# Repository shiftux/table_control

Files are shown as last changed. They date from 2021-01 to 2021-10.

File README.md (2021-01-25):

# Automating an electric standing desk
The perfect ergonomic desk solution for your prolonged home office during Covid.

Check out my article for a detailed description of the project [https://shiftux.org/making_projects/standing_desk.html](https://shiftux.org/making_projects/standing_desk.html)
### Intro
I have an electric desk that I can move from a sitting to a standing position. However I have to keep pressing a button for around 15 seconds, and then never really know exactly where to stop, since there is no top or bottom reference, except my feeling. Needless to say I decided to automate this.

### Project Video
Standing Desk Automation (https://www.youtube.com/watch?v=ZzHkn_32jh8 "Standing Desk Automation")

### State Machine
I implemented a state machine using 5 states. Where "Moving Up/Down" is used when the buttons are manually pressed (move the table a bit) and "Shift Up/Down" is used to move the table to either the top or bottom position.

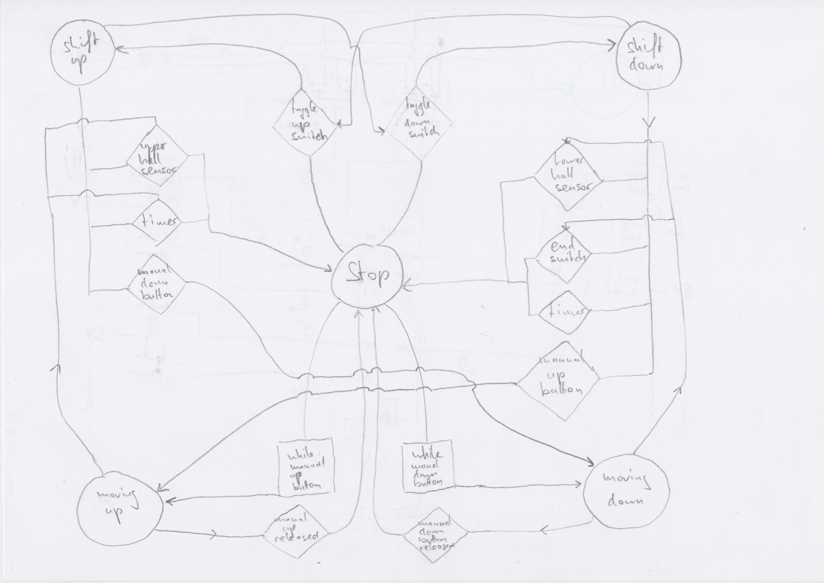
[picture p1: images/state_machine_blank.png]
The State Machine State Machine


### Wiring diagram
The wiring diagram is pretty straight forward using pull down resistors where required to prevent the Arduino from getting floating / noisy input.

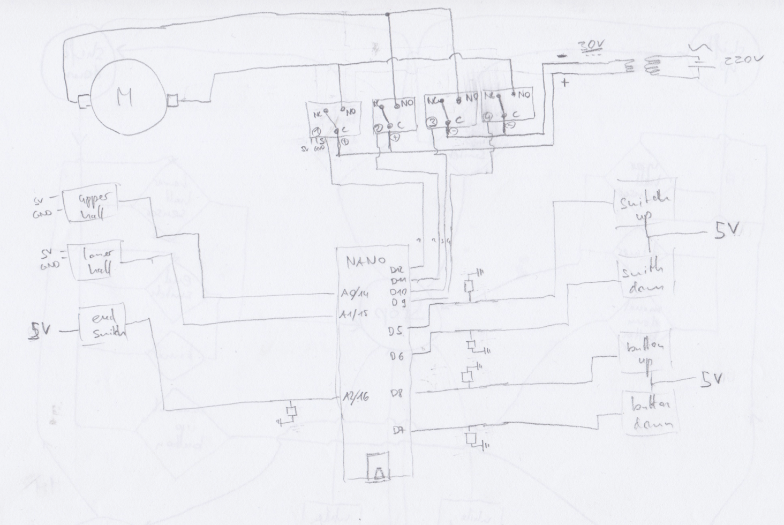
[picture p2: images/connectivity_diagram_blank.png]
The Wiring Diagram Wiring Diagram


### Components used
- 1x electric Table (and its buttons)
- 4x [Relais](https://www.conrad.ch/de/p/makerfactory-relais-modul-mf-6402384-1-st-passend-fuer-arduino-2134128.html)
- 2x [Hall sensor](https://www.conrad.ch/de/p/iduino-1485327-hallsensor-passend-fuer-einplatinen-computer-arduino-1485327.html)
- 1x [Arduino Nano](https://www.aliexpress.com/item/4000112750588.html?spm=a2g0s.9042311.0.0.27424c4dbc3uKd)
- 4x [Magnets](https://www.conrad.ch/de/p/tru-components-1572118-permanent-magnet-rund-x-h-5-mm-x-2-mm-n35eh-1-18-1-2-t-grenztemperatur-max-200-c-1572118.html)
- 1x [Switch](https://www.conrad.ch/de/p/apem-5239a-52390003-kippschalter-250-v-ac-3-a-1-x-ein-aus-ein-rastend-0-rastend-1-st-700179.html)
- 1x [Micro switch as End Switch](https://www.conrad.de/de/p/marquardt-mikroschalter-1050-5202-250-v-ac-5-a-1-x-ein-ein-tastend-1-st-703137.html)
- Loads of [DuPont Connectors](https://www.aliexpress.com/item/4000570942676.html?spm=a2g0s.9042311.0.0.27424c4dosd7NR)
- 5 10kO Resistors (pull down)
- Cable (small diameter for all the electronics and a bit larger for the relais and motor power)
- Couple of small screws
- Some of 3D printed parts (in the CAD folder)
- Micro USB Cable + Power adapter for the Arduino

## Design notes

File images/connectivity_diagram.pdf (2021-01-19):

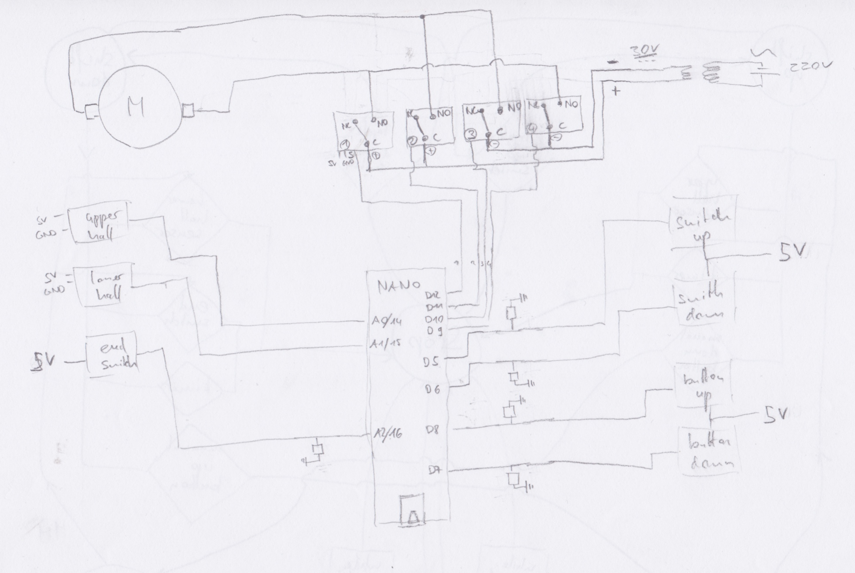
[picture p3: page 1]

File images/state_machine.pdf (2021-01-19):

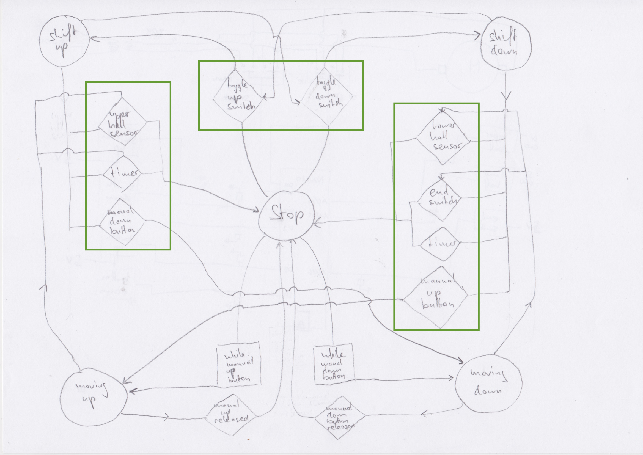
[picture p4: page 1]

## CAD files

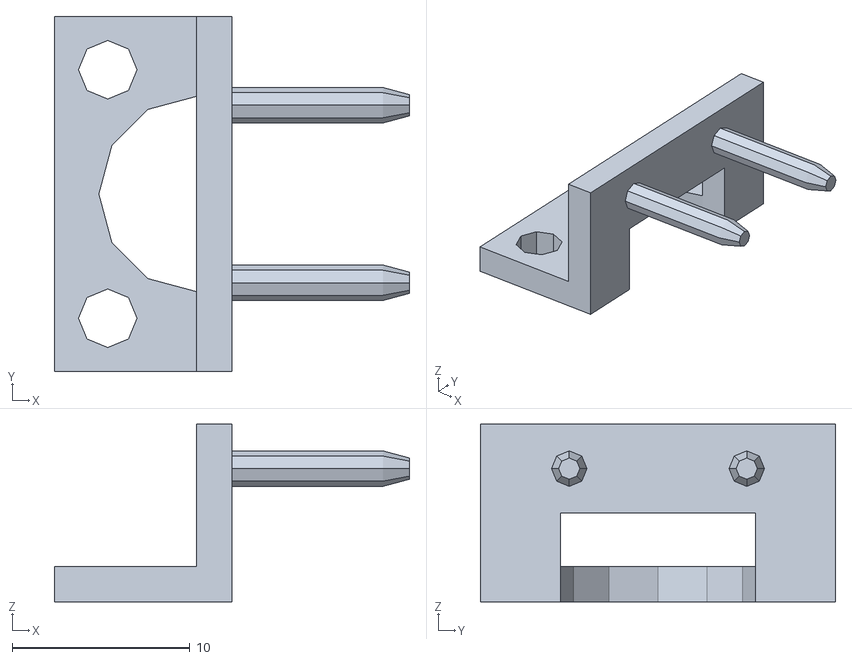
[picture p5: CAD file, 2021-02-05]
CAD/switch_holder_male.stl
20.0 x 20.0 x 10.0

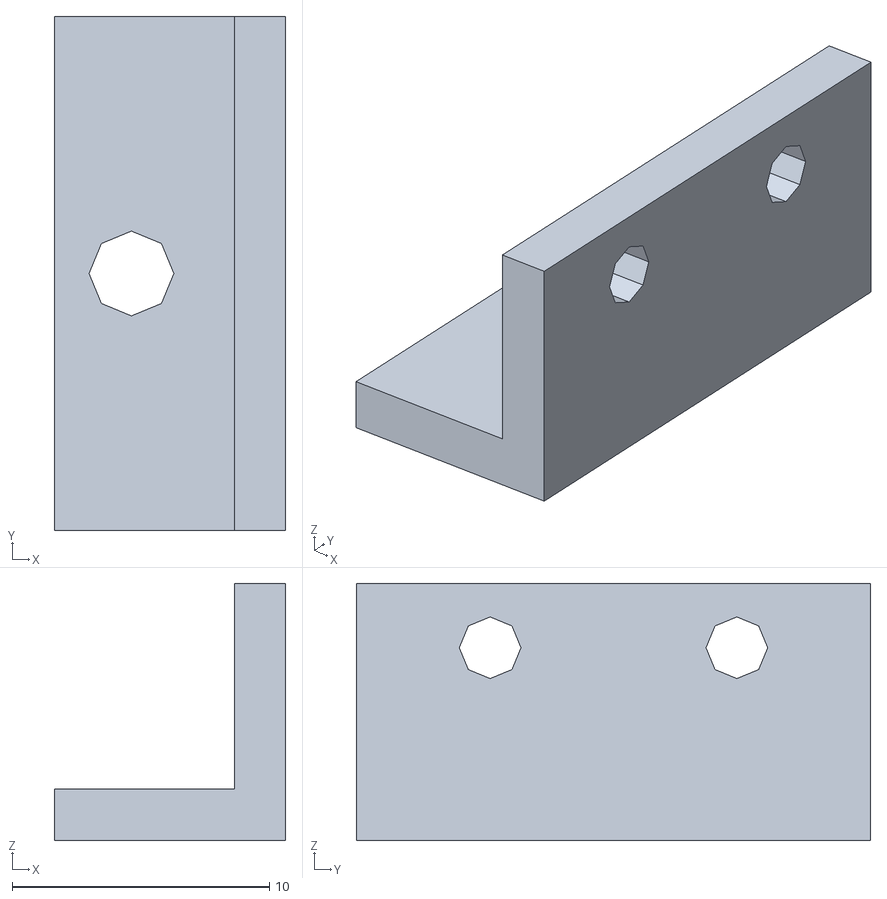
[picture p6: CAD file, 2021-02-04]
CAD/switch_holder_feemale.stl
9.00 x 20.0 x 10.0

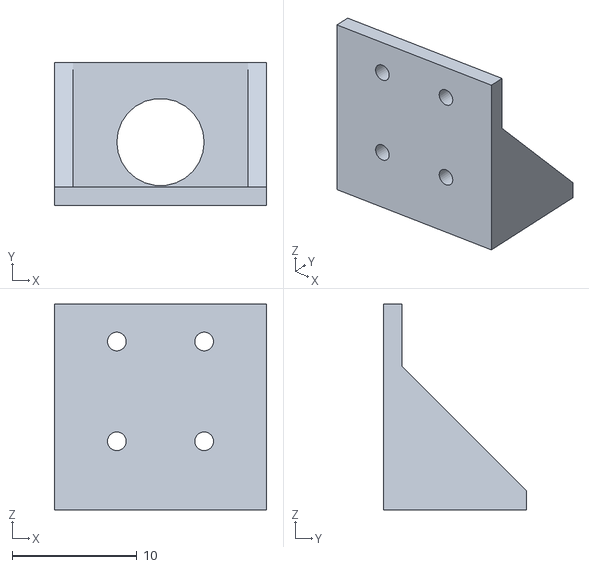
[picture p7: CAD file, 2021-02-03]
CAD/switch_holder.stl
17.0 x 11.5 x 16.5

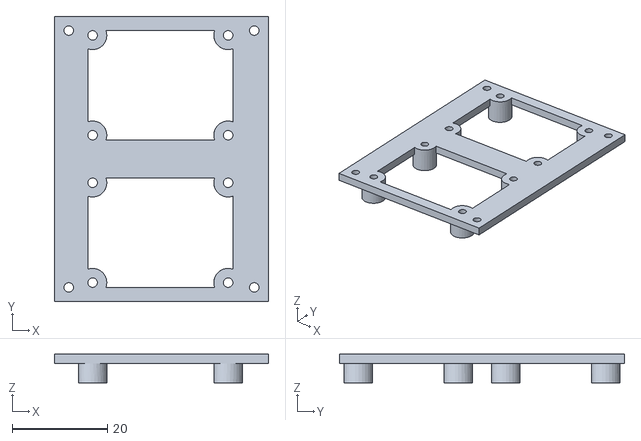
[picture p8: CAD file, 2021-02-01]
CAD/relais_holder.stl
45.0 x 60.0 x 6.00

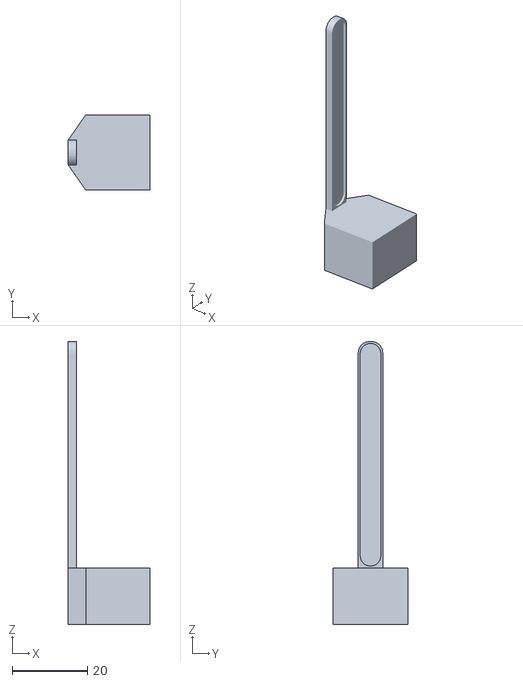
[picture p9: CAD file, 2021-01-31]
CAD/magnet_holder_lower.stl
21.7 x 20.0 x 75.0

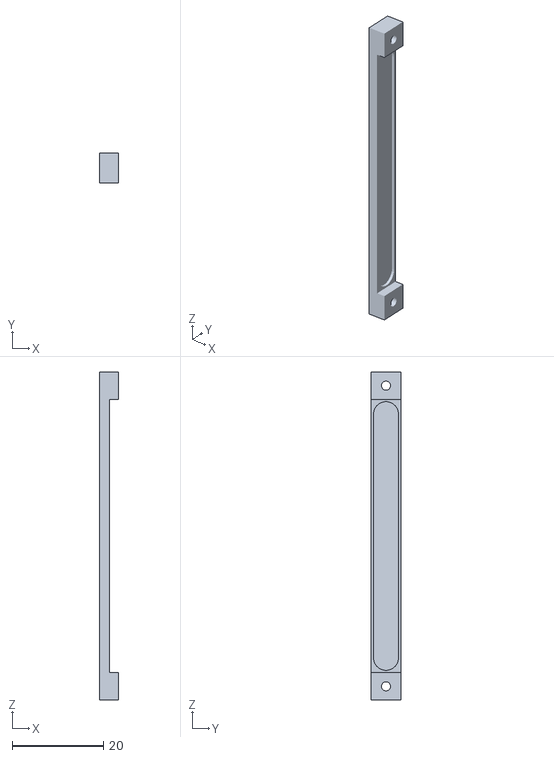
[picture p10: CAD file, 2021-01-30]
CAD/magnet_holder.stl
4.20 x 6.50 x 72.0

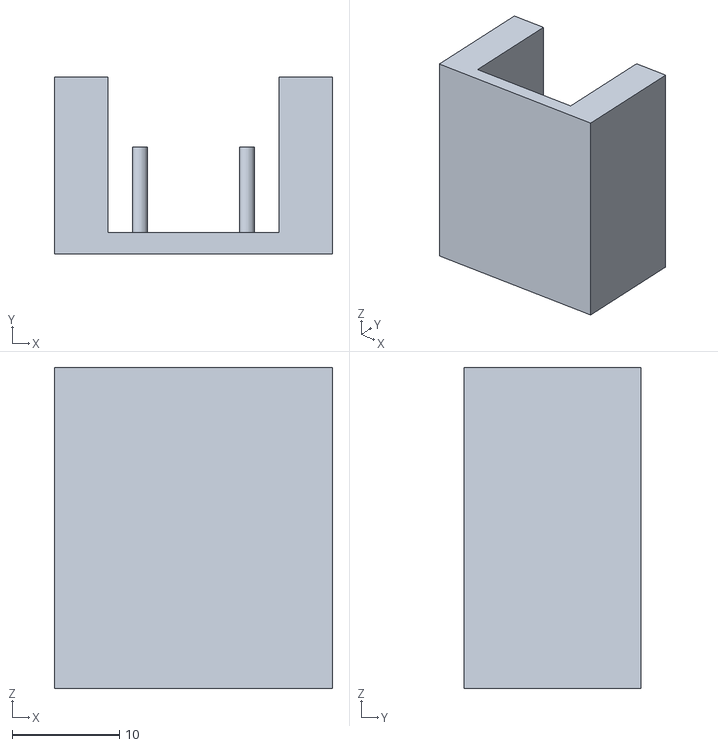
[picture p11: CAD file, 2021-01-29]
CAD/hall_sensor_holder_lower.stl
26.0 x 16.5 x 30.0

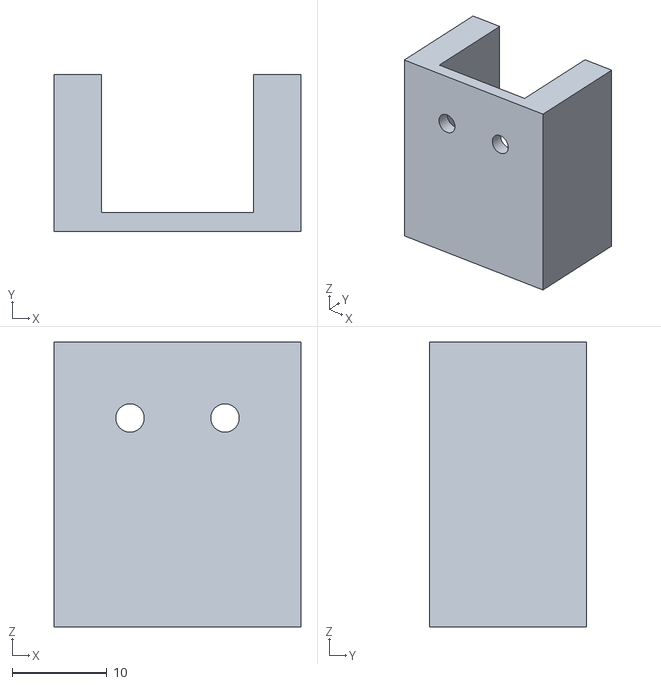
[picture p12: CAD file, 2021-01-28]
CAD/hall_sensor_holder.stl
26.0 x 16.5 x 30.0

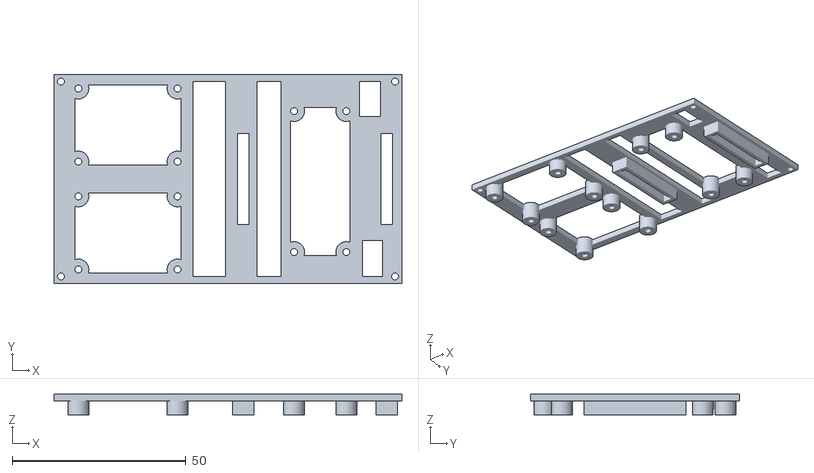
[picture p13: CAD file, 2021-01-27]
CAD/pcb_holder.stl
100.0 x 60.0 x 6.00

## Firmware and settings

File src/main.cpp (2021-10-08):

/*********************************
 * Electric table height controller
 * Author: shiftux
 * Jan 2021
 ********************************/

#include <Arduino.h>

bool debug = true;

// pin names
// pinout https://components101.com/microcontrollers/arduino-nano
#define UP_HALL_SENSOR 14
#define LOW_HALL_SENSOR 15
#define END_SWITCH 16
#define SWITCH_UP 5
#define SWITCH_DOWN 6
#define BUTTON_UP 7
#define BUTTON_DOWN 8
#define RELAIS_4 9
#define RELAIS_3 10
#define RELAIS_2 11
#define RELAIS_1 12
#define OFF 0
#define ON 1

// states
enum states {
  STOP,
  MOVING_UP,
  MOVING_DOWN,
  SHIFT_UP,
  SHIFT_DOWN
};

enum switchPositions {
  SWITCH_POS_HIGH,
  SWITCH_POS_LOW
};

// global vars
states state = STOP;
switchPositions switchPosition  = SWITCH_POS_HIGH;
int switchState = 3;
long movmentStartTime;
int upMovementTimeout = 16000; // ms
int downMovementTimeout = 13500; // ms

// switch & button state getters
int getSwitchPos(){
  if(digitalRead(SWITCH_DOWN) == 1){
    switchPosition = SWITCH_POS_LOW;
  }
  if(digitalRead(SWITCH_UP) == 1){
    switchPosition = SWITCH_POS_HIGH;
  }
  if(debug) { Serial.print("Got switch state: ");Serial.println(switchPosition); }
  return switchPosition;
};
bool switchToggleUp(){
  if(getSwitchPos() == SWITCH_POS_HIGH && switchState != SWITCH_POS_HIGH){
    switchState = SWITCH_POS_HIGH;
    return true;
  } else {
    return false;
  }
};
bool switchToggleDown(){
  if(getSwitchPos() == SWITCH_POS_LOW && switchState != SWITCH_POS_LOW){
    switchState = SWITCH_POS_LOW;
    return true;
  } else {
    return false;
  }
};
bool buttonDownActive(){
  return !digitalRead(BUTTON_DOWN);
}
bool buttonUpActive(){
  return !digitalRead(BUTTON_UP);
}

// motor movements
void motorStop(){
  digitalWrite(RELAIS_1, OFF);
  digitalWrite(RELAIS_2, OFF);
  digitalWrite(RELAIS_3, OFF);
  digitalWrite(RELAIS_4, OFF);
};
void motorMoveUp(){
  motorStop();
  digitalWrite(RELAIS_1, ON);
  digitalWrite(RELAIS_3, ON);
};
void motorMoveDown(){
  motorStop();
  digitalWrite(RELAIS_2, ON);
  digitalWrite(RELAIS_4, ON);
};
void stop(){
  motorStop();
  if(debug) { Serial.println("Setting state: STOP"); }
  state = STOP;
};

// limit checks
bool hitLowerLimit(){
  if (digitalRead(LOW_HALL_SENSOR) == 0){ // hall sensor is 0 when magnet is present
    if(debug) { Serial.println("Hit lower hall sensor"); }
    return true;
  }
  else if (digitalRead(END_SWITCH) == 1){
    if(debug) { Serial.println("Hit lower lower end switch"); }
    return true;
  }
  else {
    return false;
  }
};
bool hitUpperLimit(){
  if (digitalRead(UP_HALL_SENSOR) == 0){
    if(debug) { Serial.println("Hit upper hall sensor"); }
    return true;
  }
  else {
    return false;
  }
};
bool downTimeoutHit(){
  if (millis() - movmentStartTime > downMovementTimeout){
    if(debug) { Serial.println("Hit down time limit timeout"); }
    return true;
  } else {
    return false;
  }
};
bool upTimeoutHit(){
  if (millis() - movmentStartTime > upMovementTimeout){
    if(debug) { Serial.println("Hit up time limit timeout"); }
    return true;
  } else {
    return false;
  }
};

// state actions
void stopActions(){
  motorStop();
  if (switchToggleDown()){
    if(debug) { Serial.println("Setting state: SHIFT_DOWN"); }
    state = SHIFT_DOWN;
  }
  else if (switchToggleUp()){
    if(debug) { Serial.println("Setting state: SHIFT_UP"); }
    state = SHIFT_UP;
  }
  else if (buttonDownActive()){
    if(debug) { Serial.println("Setting state: MOVING_DOWN"); }
    state = MOVING_DOWN;
  }
  else if (buttonUpActive()){
    if(debug) { Serial.println("Setting state: MOVING_UP"); }
    state = MOVING_UP;
  }
  else {
    if(debug) { Serial.println("Setting state: STOP"); }
    state = STOP;
  }
  movmentStartTime = millis();
};

void movingUpActions(){
  if (hitUpperLimit()){
    if(debug) { Serial.println("not moving up: found upper limit"); }
    stop();
  }
  else if (!buttonUpActive()){
    if(debug) { Serial.println("not moving up: button released"); }
    stop();
  }
  else {
    if(debug) { Serial.println("moving up"); }
    motorMoveUp();
  }
};

void movingDownActions(){
  if (hitLowerLimit()){
    if(debug) { Serial.println("not moving down: found lower limit"); }
    stop();
  }
  else if (!buttonDownActive()){
    if(debug) { Serial.println("not moving down: button released"); }
    stop();
  }
  else {
    if(debug) { Serial.println("moving down"); }
    motorMoveDown();
  }
};

void shiftUpActions(){
  if (hitUpperLimit()){
    stop();
  }
  else if (upTimeoutHit()){
    stop();
  }
  else if (switchToggleDown()){
    motorStop();
    state = SHIFT_DOWN;
  }
  else if (buttonDownActive()){
    motorStop();
    state = MOVING_DOWN;
  }
  else{
    motorMoveUp();
  }
};

void shiftDownActions(){
  if (hitLowerLimit()){
    stop();
  }
  else if (downTimeoutHit()){
    stop();
  }
  else if (switchToggleUp()){
    motorStop();
    state = SHIFT_UP;
  }
  else if (buttonUpActive()){
    motorStop();
    state = MOVING_UP;
  }
  else{
    motorMoveDown();
  }
};

void my_init(){
  pinMode(UP_HALL_SENSOR, INPUT);
  pinMode(LOW_HALL_SENSOR, INPUT);
  pinMode(END_SWITCH, INPUT);
  pinMode(SWITCH_UP, INPUT);
  pinMode(SWITCH_DOWN, INPUT);
  pinMode(BUTTON_UP, INPUT);
  pinMode(BUTTON_DOWN, INPUT);
  pinMode(RELAIS_1, OUTPUT);
  pinMode(RELAIS_2, OUTPUT);
  pinMode(RELAIS_3, OUTPUT);
  pinMode(RELAIS_4, OUTPUT);
}

void setup() {
  my_init();
  if(debug) { Serial.begin(9600); }// open the serial port at 9600 bps
  switchState = getSwitchPos();
  movmentStartTime = millis();
  stop();
}

// main loop
void loop() {
  if (state == STOP) {
    stopActions();
  }
  else if (state == MOVING_UP) {
    movingUpActions();
  }
  else if (state == MOVING_DOWN) {
    movingDownActions();
  }
  else if (state == SHIFT_UP) {
    shiftUpActions();
  }
  else if (state == SHIFT_DOWN) {
    shiftDownActions();
  }
  else{
    stop();
  }
}

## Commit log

2021-01-10 buttons and switch working
2021-01-11 tested on prototype
2021-01-13 hall sensors are low when magnet is close
2021-01-14 switched to 4 relais layout
